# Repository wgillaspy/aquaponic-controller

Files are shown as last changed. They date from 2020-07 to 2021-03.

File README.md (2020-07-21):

# aquaponic-controller

*Currently a trough style hydroponic setup while I work out the hardware and code.  Once the bugs
are fixed and things stabilize, if the space is available, I'll add in some fish.  But right it's
easy enough to grow a decent crop of lettuce with General Hydroponics fertilizer, epsom salt, calcium hydroxide
and some ferrous gluconate iron solution.

This isn't a particularly cheap project to undertake, but the results have been been rewarding.
Fresh, well developed, and bug free lettuce and herbs.  Being in South Carolina, lettuce isn't
one of those things we get to grow well in the summer. Simply too hot.  Now we have a surpus for ourselves
and friends.

As with most of my projects, this one involves a raspberry pi and an arduino.  Adding to the cast
is also a Alchitry Au (which I may regret since I can't seen to find any more to order) and several
Atlas Scientific circuits and probes.  Binding those circuits to the raspberry pi is a whitebox labs
Tentacle T3.

[The full bill of materials is here.](BOM.MD)

I really can't speak highly enough of the Atlas Scientific ecosystem.  With a little looking around
I was able to find enough information to drive the circuits with javascript, pop them into a NodeJs
project and then pop that into a docker container.

I prefer to run ubuntu server on my raspberry pi, so there was some additional configuration
I needed to enable the I2C interface.

If you dig ansible, you can use this block to help figure out how to enable I2C on a ubuntu install.
I've also included the two files that are copied in the root of this project.

```yaml
    - name: Install i2c-tools
      apt:
        name: i2c-tools
        state: present
        update_cache: yes
      become: yes
    - name: Copy modules file.
      copy:
        src: modules
        dest: /etc/modules
        mode: 0644
      become: yes
    - name: Copy the usrcfg.txt to the firmware directory.
      copy:
        src: usercfg.txt
        dest: /boot/firmware/usercfg.txt
        mode: 0655
      become: yes
```

The [parts](parts) directory contains all the .stls and Alibre files that I used to mount things.  Nothing is refined, but all 
the electronics and pumps mount to DIN rails.  The probes and float switches mount to 1"PVC pipes in the sump.

 #### State of the project.
- pH is monitored and adjusted upward with calcium hydroxide solution in tap water.  The clear liquid between the calcium sediment
  and crust is dosed using a Milwaukee Dosing controlled through Home Assistant > Phillips Hue > Smart Plug.
- Electrical Conductivity (EC) is monitored and adjusted upward by dosing diluted General Hydroponic fertilizer with an EZO PMP. 
- A diluted mixture of Magnesium (epsom salt) and Iron (ferrous gluconate) is dosed periodically with an EZO PMP.  Iron and Magnesium are not 
  monitored and are simply added on a set schedule.
  
The configuration is pretty strait forward and [available here](src/main/javascript/probe-reader/configuration.json) 

Probes are easily added to the configuration by adding a new distinct element to the probe object.  If the new probe
needs to run some dosing pump, then a rule can be setup in the dosing section with the same distinct element key.

Dosing pumps that run a schedule can be added to the scheduled section of the configuration.

Again, I can't really speak more highly of the Atlas Scientific ecosystem.  Once the boiler plate has been accomplished, its super easy to add additional functionality.

And as usual, I use splunk to log readings.

The arduino currently only holds the Alchitry pins low, but it will eventually be used to automate the periodic water changes.

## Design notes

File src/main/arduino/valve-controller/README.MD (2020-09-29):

lsusb -v | grep -i 'Arduino Uno'

SUBSYSTEMS=="usb", ATTRS{serial}=="7583331353335180F132", SYMLINK+="ino"  > /etc/udev/rules.d/99-usb.rules

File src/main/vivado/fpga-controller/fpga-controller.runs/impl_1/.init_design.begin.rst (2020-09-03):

<?xml version="1.0"?>
<ProcessHandle Version="1" Minor="0">
    <Process Command=".planAhead." Owner="William" Host="DCOMP" Pid="9704">
    </Process>
</ProcessHandle>

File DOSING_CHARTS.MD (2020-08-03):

### Nutrient
| | Type | ml | Conductivity | Total EC | 
|---|--- |----- | --- | ---|
| Full Change | Water |? | 179 | 179 | 
| Full Change | Flora Grow |250 | 400 | 584 | 
| Full Change | Flora Micro |150 | 464 | 1046 |
| Full Change | Flora Cal Mag |50 | ? | ? |

- nutrient_one   = Flora Grow  
- nutrient_three = Flora Micro  
- nutrient_four  = Kelp extract  

### Dosing reservoir mix 840mL (nutrient_two) Iron and Magnesium:  
640ml filtered water  
100ml Mg  
100ml Fe

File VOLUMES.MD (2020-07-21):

### Trough Volume By Depth
| Depth | Gallons  | 
|---|---|
| 3" | 20  |
| 3.5"  | 23  |
| 4" | 26 |
| 5" | 33 |

### Current Volumes:
| | Gallons  | 
|---  |---|
| Upper | 23  |
| Lower | 26 |
| Sump | 33 |
| Total | 59 |

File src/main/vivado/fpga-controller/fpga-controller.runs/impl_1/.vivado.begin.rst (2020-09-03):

<?xml version="1.0"?>
<ProcessHandle Version="1" Minor="0">
    <Process Command="vivado.bat" Owner="William" Host="DCOMP" Pid="14076" HostCore="8" HostMemory="017047703552">
    </Process>
</ProcessHandle>
<?xml version="1.0"?>
<ProcessHandle Version="1" Minor="0">
    <Process Command="vivado.bat" Owner="William" Host="DCOMP" Pid="6972" HostCore="8" HostMemory="017047703552">
    </Process>
</ProcessHandle>

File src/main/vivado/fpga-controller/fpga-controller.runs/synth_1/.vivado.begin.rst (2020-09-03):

<?xml version="1.0"?>
<ProcessHandle Version="1" Minor="0">
    <Process Command="vivado.bat" Owner="William" Host="DCOMP" Pid="12516" HostCore="8" HostMemory="017047703552">
    </Process>
</ProcessHandle>

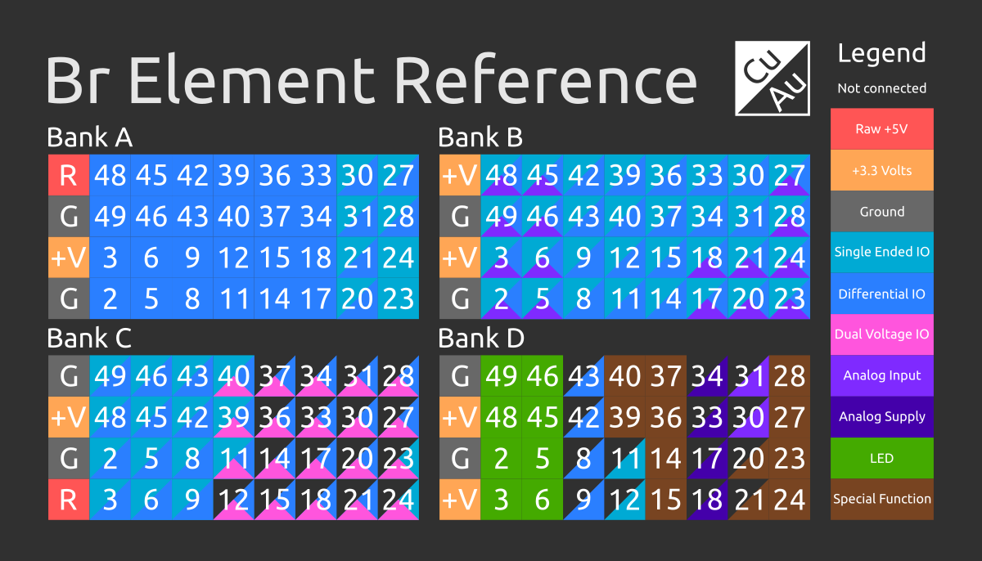
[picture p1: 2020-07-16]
documents/br_front.png

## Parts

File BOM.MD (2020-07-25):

#### Things:
- [Horizontal Leg tank](https://www.tractorsupply.com/tsc/product/horizontal-leg-tank-65-gal) with the top trimmed off. (used)
- Costco Industrial Storage Rack $159.00 
- [Trough Liner](https://farmplasticsupply.com/hydroponics?product_id=474)                   $36.99
- [Blue Line Pump](https://www.championlighting.com/blueline_40_hd_external_water_pump.html) $212.00
- Plywood and 1/8 Boards $80.00
- Raspberry Pi 3b+ (On hand)
- [Milwaukee Dosing pump](https://milwaukeeinstruments.com/milwaukee-instruments-mp810-dosing-pump-for-ph-controller/) x $87.00
- [Smart Plugs](https://www.amazon.com/gp/product/B07SQGG8Z7/ref=ppx_yo_dt_b_asin_title_o08_s00?ie=UTF8&psc=1) (2) $34.99
- [Phlizon 600W LED](https://www.amazon.com/gp/product/B0752CL6KJ/ref=ppx_yo_dt_b_asin_title_o08_s00?ie=UTF8&psc=1) x 3 $239.97
- [T5 HO 4FT 4 Lamp Horticultural Fixture – Red Bloom Spectrum](https://www.activegrowled.com/hydroponic-supplies/t5-ho-4ft-4-lamp-horticultural-fixture-red-bloom-spectrum/) x 2 $438.00
- [T8 HO 4FT 4 Lamp Horticultural Fixture – Sun White Spectrum](https://www.activegrowled.com/hydroponic-supplies/t8-ho-4ft-4-lamp-horticultural-fixture-sun-white-spectrum/) x 2 $438.00
- [T8 HO 2FT 4 Lamp Horticultural Fixture – Red Bloom Spectrum](https://www.activegrowled.com/hydroponic-supplies/t8-ho-2ft-4-lamp-horticultural-fixture-red-bloom-spectrum/) x 2 $270.00
- [U.S. Solid Stainless Steel Electrical Ball Valve 2 Wire Reverse Polarity](https://ussolid.com/u-s-solid-motorized-ball-valve-1-stainless-steel-electrical-ball-valve-with-full-port-9-24-v-dc-2-wire-reverse-polarity.html) x 1 52.99
- [U.S. Solid Motorized Ball Valve 2 Wire Auto Return](https://ussolid.com/u-s-solid-motorized-ball-valve-1-stainless-steel-electrical-ball-valve-with-full-port-9-24-v-ac-dc-2-wire-auto-return.html) x 2 $125.98

Atlas Scientific specific products:
- [EZO-PMP™ Embedded Dosing Pump](https://atlas-scientific.com/peristaltic/) × 2 $170.00
- [EZO™ RTD Temperature Circuit](https://atlas-scientific.com/temperature/) × 1	  $28.00
- [PT-1000 Temperature Probe](https://atlas-scientific.com/temperature/) × 1	      $20.00
- [Whitebox Labs Tentacle T3](https://atlas-scientific.com/carrier-boards/whitebox-labs-tentacle-t3/) × 2	     $210.00
- [EZO™ pH Circuit](https://atlas-scientific.com/ph/) x 1                 $40.00
- [Lab Grade pH Probe](https://atlas-scientific.com/ph/) x 1              $75.00
- [EZO™ Conductivity Circuit](https://atlas-scientific.com/conductivity/)  x 1      $60.00
- [Conductivity Probe K 1.0](https://atlas-scientific.com/conductivity/)   x 1     $139.00

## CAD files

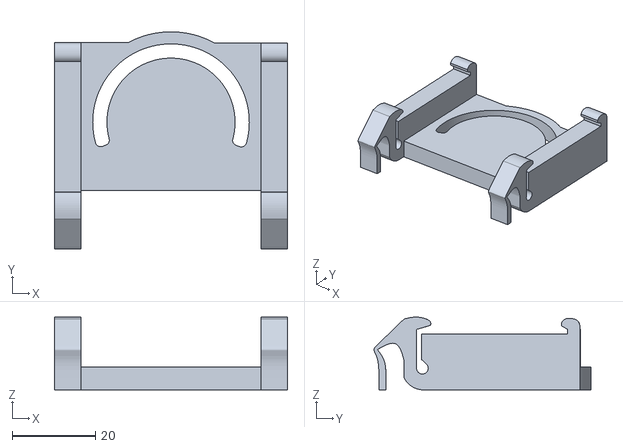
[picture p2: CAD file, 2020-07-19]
parts/PumpAssembly.stl
55.9 x 52.1 x 17.5

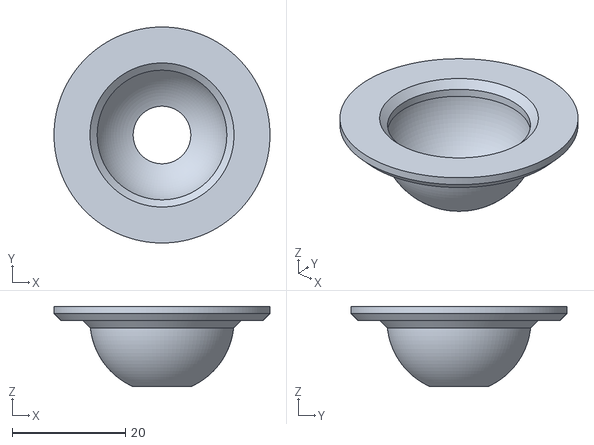
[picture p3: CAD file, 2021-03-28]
parts/Basket.stl
38.1 x 38.1 x 14.2

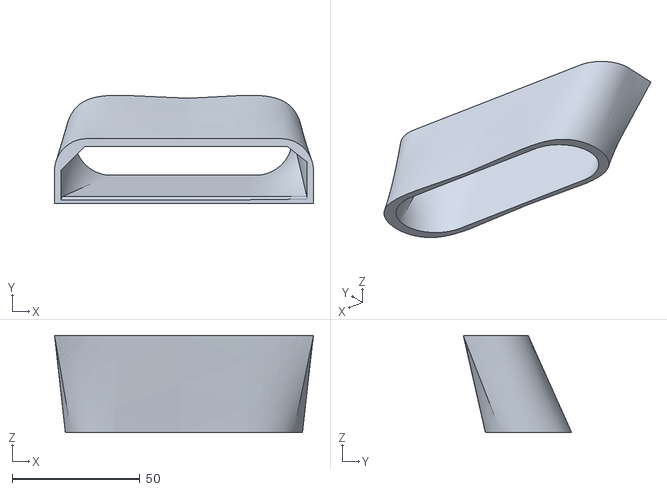
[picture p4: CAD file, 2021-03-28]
parts/Cleaner/FrontSiphone.stl
101.5 x 42.5 x 38.1

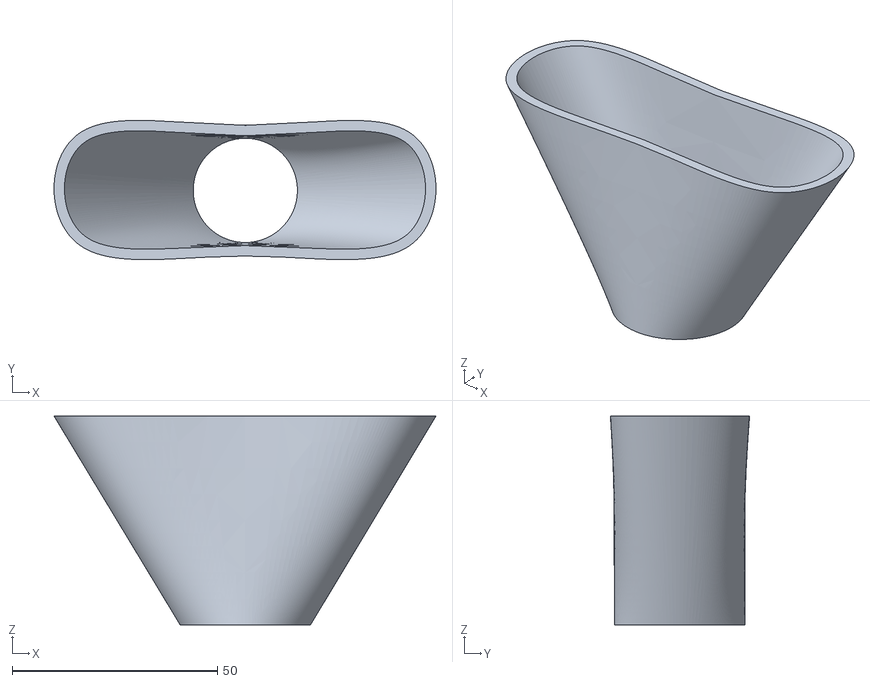
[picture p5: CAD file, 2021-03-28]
parts/Cleaner/RearSiphon.stl
93.0 x 33.9 x 50.8

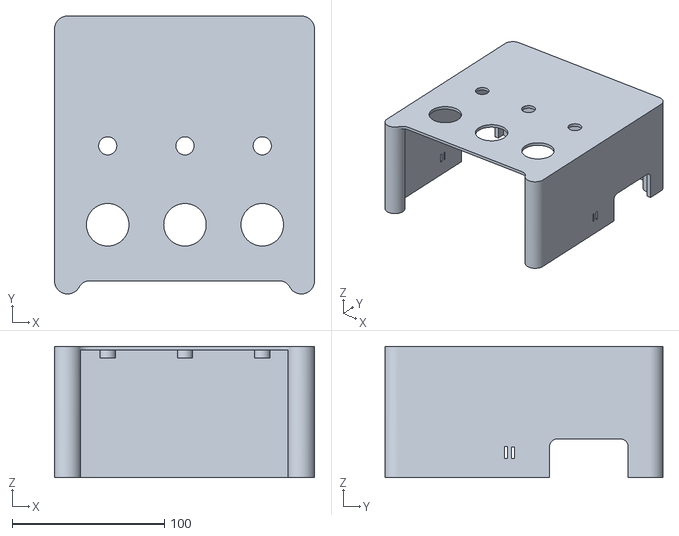
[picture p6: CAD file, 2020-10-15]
parts/ControlBoxLidWSkirt.stl
170.9 x 182.7 x 86.4

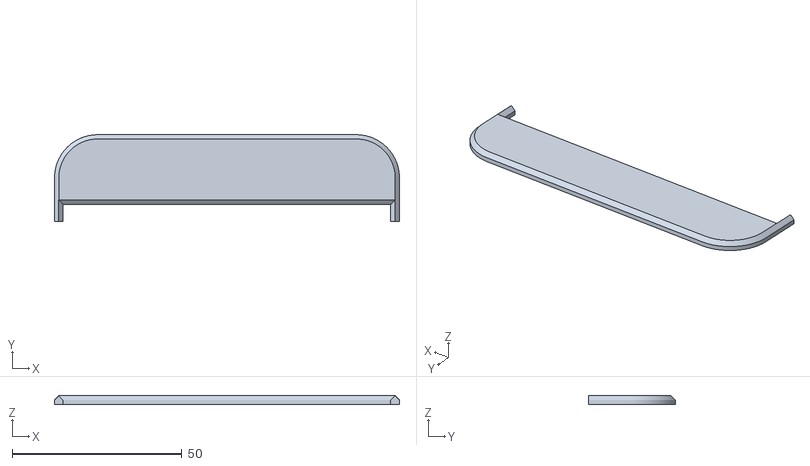
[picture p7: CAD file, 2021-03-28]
parts/Cleaner/FrontCover.stl
101.5 x 25.5 x 2.54

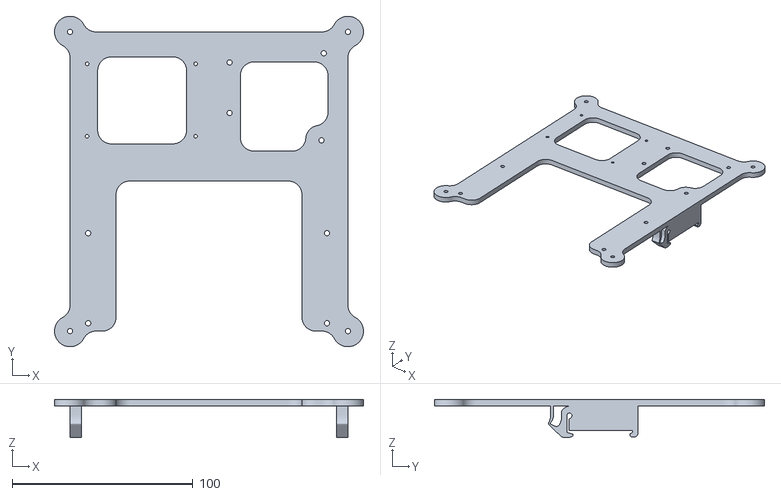
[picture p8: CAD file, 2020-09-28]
parts/ValveControlBackPlate.stl
170.9 x 182.7 x 21.3

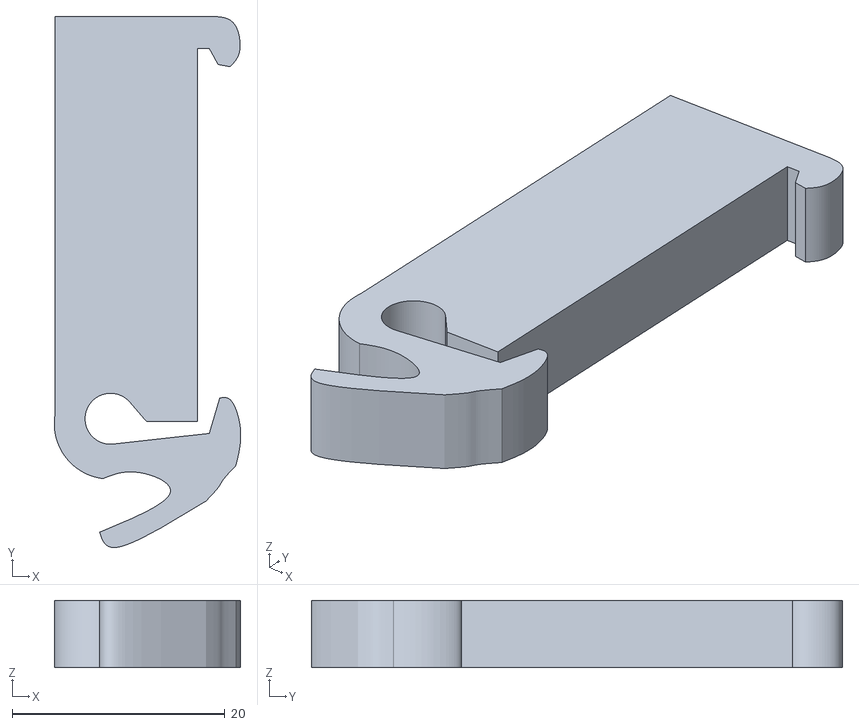
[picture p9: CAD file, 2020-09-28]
parts/DIN_RAIL_MOUNT.stl
17.5 x 50.0 x 6.35

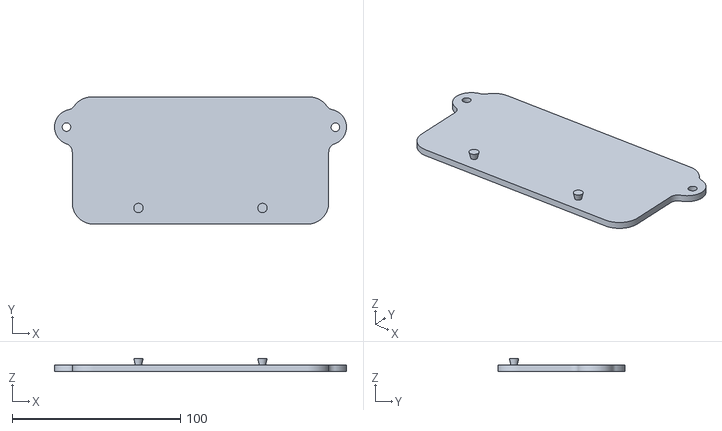
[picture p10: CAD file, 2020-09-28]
parts/Ubiq8PortMount.stl
173.5 x 75.6 x 7.62

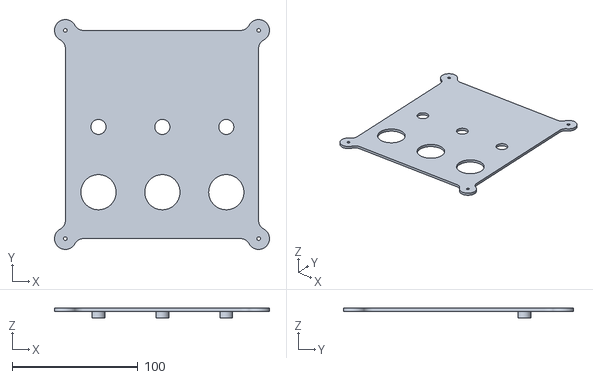
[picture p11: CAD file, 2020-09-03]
parts/ControlBoxLid.stl
170.9 x 182.7 x 7.62

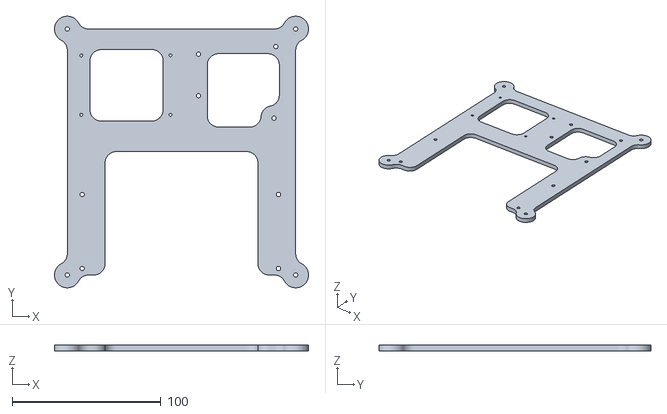
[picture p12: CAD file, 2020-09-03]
parts/ArduinoAlchitryRelayProto.stl
170.9 x 182.7 x 3.81

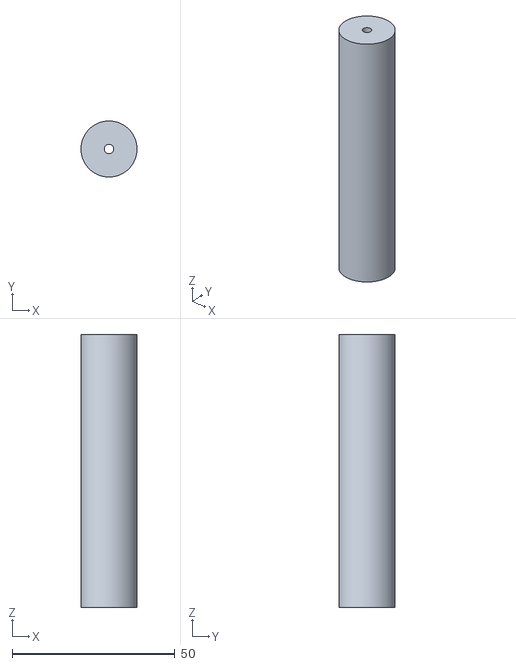
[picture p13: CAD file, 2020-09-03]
parts/Riser.stl
17.2 x 17.2 x 83.8

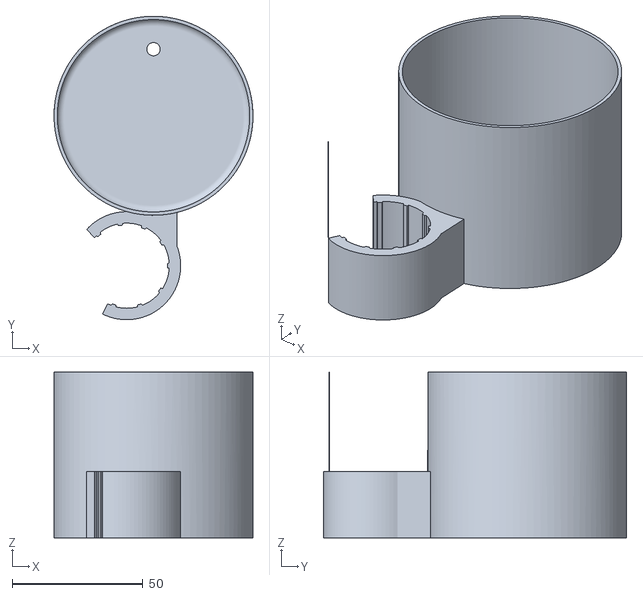
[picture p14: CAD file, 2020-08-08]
parts/floatWaveProtector.stl
76.2 x 116.2 x 63.5

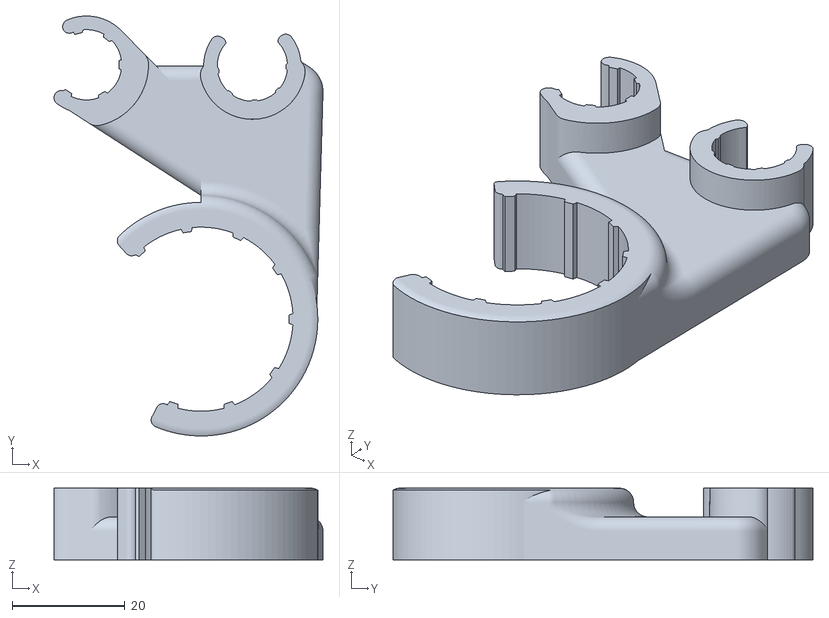
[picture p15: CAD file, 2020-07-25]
parts/probePipeHold.stl
47.6 x 74.4 x 12.7

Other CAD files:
parts/floatPipeHold.stl
parts/pipeHold.stl
parts/pipeTop.stl
parts/PlateDINAssm.stl
parts/8ch_relay_board.stl
parts/MotorMount.stl
parts/Washer.stl
parts/airlineConnector.stl
parts/alchitryAuPlate.stl
parts/alchitry_din.stl

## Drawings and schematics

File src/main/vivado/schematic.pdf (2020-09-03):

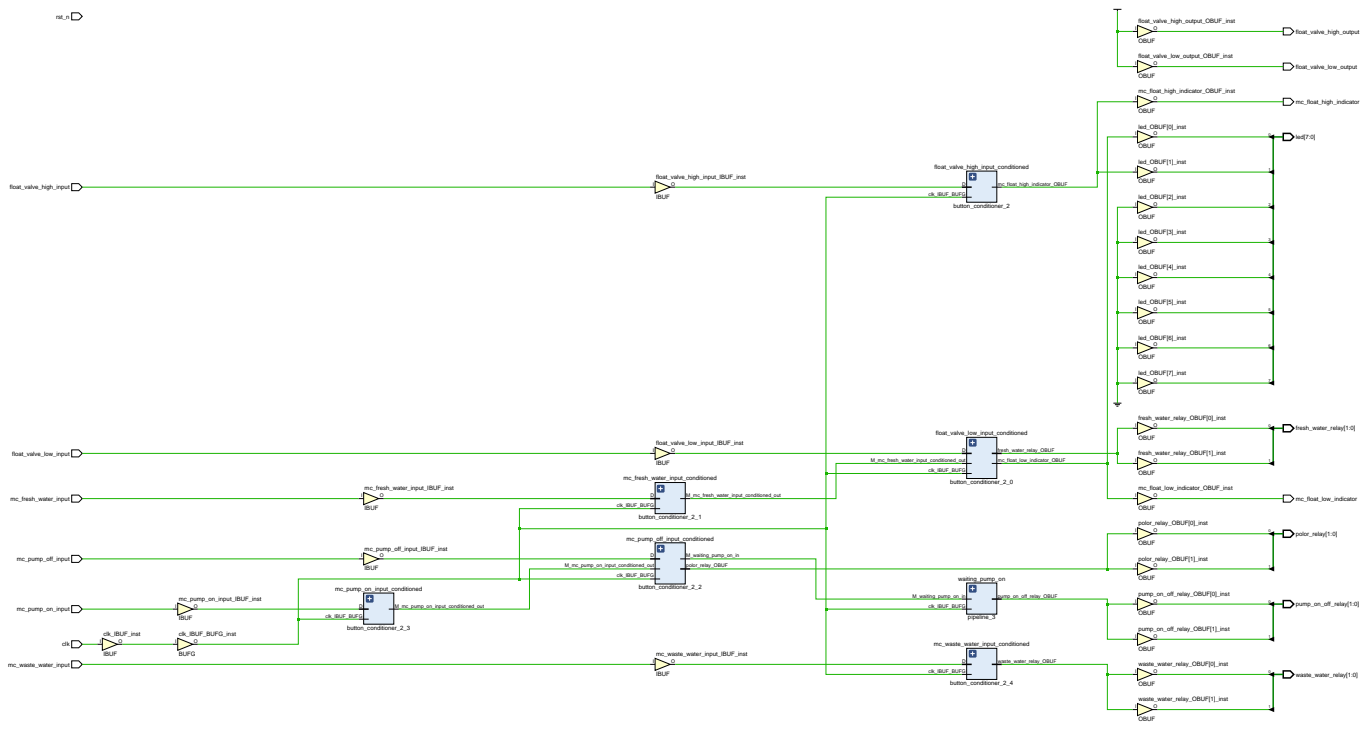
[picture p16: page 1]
float_valve_high_input; float_valve_low_input; mc_fresh_water_input; mc_pump_off_input; mc_pump_on_input; clk; mc_waste_water_input; clk_IBUF_inst; IBUF; mc_pump_on_input_IBUF_inst; clk_IBUF_BUFG_inst; BUFG; mc_fresh_water_input_IBUF_inst; mc_pump_off_input_IBUF_inst; button_conditioner_2_3; clk_IBUF_BUFG; float_valve_high_input_IBUF_inst; float_valve_low_input_IBUF_inst; mc_fresh_water_input_conditioned; button_conditioner_2_1; M_mc_fresh_water_input_conditioned_out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

polor_relay_OBUF

mc_pump_on_input_conditioned | M_mc_pump_on_input_conditioned_out

clk_IBUF_BUFG | M_waiting_pump_on_in | waiting_pump_on

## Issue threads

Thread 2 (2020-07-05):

Change pH dosing to be a time based process rather than waiting on polling to turn it back off.

wgillaspy, 2020-07-05:

wgillaspy, 2021-03-28:
Fixed with ezo dosing pump.

Closed 2021-03-28.

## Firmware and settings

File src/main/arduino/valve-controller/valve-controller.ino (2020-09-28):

#include <ArduinoJson.h>

#define VALVE_OPEN_CLOSE_DELAY 10000
#define WAIT_DELAY 100


#define LED_AND_POWER_INDICATOR           13

#define LED_ONE   A5
#define LED_TWO   A4
#define LED_THREE A3

int LED_VALUE = 130;

// The valves
#define FRESH_WATER_VALVE                 12
#define WASTE_WATER_VALVE                 11
#define FLOW_WATER_VALVE_POLARITY         10
#define FLOW_WATER_VALVE_ON_OFF            9

// The buttons
#define BUTTON_GREEN   A0
#define BUTTON_YELLOW  A1
#define BUTTON_RED     A2

// The float switch inputs
#define FLOAT_SWITCH_LOWER 8
#define FLOAT_SWITCH_UPPER 7


// OLD BELOW / USED ABOVE

boolean flowWaterStatus = true;

boolean waterChange = false;

int loopCount = 0;
int  freshWaterValveState = 0;
int wasteWaterValveState = 0;
int flowValveState = 0;

int floatSwitchLowerValue = 0;
int floatSwitchUpperValue = 0;

boolean override = false;




void setup() {

   Serial.begin(9600);

   pinMode(LED_ONE, OUTPUT);
   pinMode(LED_TWO, OUTPUT);
   pinMode(LED_THREE, OUTPUT);

   analogWrite(LED_ONE, 0);
   analogWrite(LED_TWO, 0);
   analogWrite(LED_THREE, 0);
  
   pinMode(LED_AND_POWER_INDICATOR, OUTPUT);
   digitalWrite(LED_AND_POWER_INDICATOR, HIGH);

   pinMode(FRESH_WATER_VALVE, OUTPUT);
   digitalWrite(FRESH_WATER_VALVE, LOW);

   pinMode(WASTE_WATER_VALVE, OUTPUT);
   digitalWrite(WASTE_WATER_VALVE, LOW);

   pinMode(FLOW_WATER_VALVE_POLARITY, OUTPUT);
   digitalWrite(FLOW_WATER_VALVE_ON_OFF, LOW);

   pinMode(FLOW_WATER_VALVE_ON_OFF, OUTPUT);
   digitalWrite(FLOW_WATER_VALVE_ON_OFF, LOW);

   pinMode(BUTTON_GREEN, INPUT);
   pinMode(BUTTON_YELLOW, INPUT);
   pinMode(BUTTON_RED, INPUT);

   pinMode(FLOAT_SWITCH_LOWER, INPUT);
   pinMode(FLOAT_SWITCH_UPPER, INPUT);

   turnOnFlowValve();
}

void loop() {

  loopCount++;
  delay(WAIT_DELAY);

  if (Serial.available() > 0) {
    // read the incoming byte:
    String incomingJson = Serial.readString();
    readJsonAndDoAction(incomingJson);
    
  }

   floatSwitchLowerValue = digitalRead(FLOAT_SWITCH_LOWER);
   floatSwitchUpperValue = digitalRead(FLOAT_SWITCH_UPPER);
   
   int buttonGreenValue = digitalRead(BUTTON_GREEN);
   int buttonYellowValue = digitalRead(BUTTON_YELLOW);
   int buttonRedValue = digitalRead(BUTTON_RED);

   if (buttonGreenValue > 0) {
     override = false;
     toggleFreshWaterValue(buttonGreenValue);
   } else {
     if (!override) {
      toggleFreshWaterValue(buttonGreenValue);
     }
   }

   if (buttonYellowValue > 0) {
     override = false;
     if (flowWaterStatus) {
       turnOffFlowValve();
     } else {
       turnOnFlowValve();
     }
   }

   if (buttonRedValue > 0) {
     override = false;
     toggleWasteWaterValue(buttonRedValue);
   } else {
    if (!override) {
     toggleWasteWaterValue(buttonRedValue);
    }
   }

   if (loopCount > 10) {
     serialWriteJsonValues();
     loopCount = 0;
  }
}

void indicatorLedOn(int LED) {
  analogWrite(LED, LED_VALUE);
}

void indicatorLedOff(int LED) {
  analogWrite(LED, 0);
}

void readJsonAndDoAction(String inputJson) {
    StaticJsonDocument<400> doc;
    DeserializationError error = deserializeJson(doc, inputJson);
    // Test if parsing succeeds.
    if (error) {
      Serial.print(F("deserializeJson() failed: "));
      Serial.println(error.c_str());
      return;
    }
    int desiredflowValveState = doc["fvs"];
    int desiredFreshwaterValveState = doc["fws"];
    int desiredWasteWaterValveState = doc["wws"];;



    toggleFreshWaterValue(desiredFreshwaterValveState);
    toggleWasteWaterValue(desiredWasteWaterValveState);

    if (desiredflowValveState > 0) {
      turnOnFlowValve();
    } else {
      turnOffFlowValve();
    }

    override = true;

}

void serialWriteJsonValues() {
      String sendJson = "";

      String floatSwitchLowerJson = getJsonPair("fsl", floatSwitchLowerValue);
      String floatSwitchUpperJson = getJsonPair("fsu", floatSwitchUpperValue);
      String flowValveStateJson = getJsonPair("fvs",   flowValveState);

      String freshWaterValveStateJson = getJsonPair("fws", freshWaterValveState);
      String wasteWaterValveStateJson = getJsonPair("wws", wasteWaterValveState);

      sendJson = addToJsonString(sendJson, floatSwitchLowerJson);
      sendJson = addToJsonString(sendJson, floatSwitchUpperJson);
      sendJson = addToJsonString(sendJson, flowValveStateJson);
      sendJson = addToJsonString(sendJson, freshWaterValveStateJson);
      sendJson = addToJsonString(sendJson, wasteWaterValveStateJson);

      Serial.println(sendJson);
}

void toggleFreshWaterValue(int state) {
    if (state > 0) {
      indicatorLedOn(LED_ONE);
      digitalWrite(FRESH_WATER_VALVE, HIGH);
      
    } else {
      indicatorLedOff(LED_ONE);
      digitalWrite(FRESH_WATER_VALVE, LOW);
    }
    freshWaterValveState = state;
}

void toggleWasteWaterValue(int state) {
    if (state > 0) {
      indicatorLedOn(LED_TWO);
      digitalWrite(WASTE_WATER_VALVE, HIGH);
      
    } else {
      indicatorLedOff(LED_TWO);
      digitalWrite(WASTE_WATER_VALVE, LOW);
    }
    wasteWaterValveState = state;
}


void turnOffFlowValve() {
    indicatorLedOn(LED_THREE);
    digitalWrite(FLOW_WATER_VALVE_ON_OFF, LOW);
    delay(WAIT_DELAY);
    digitalWrite(FLOW_WATER_VALVE_POLARITY, LOW);
    delay(WAIT_DELAY);
    digitalWrite(FLOW_WATER_VALVE_ON_OFF, HIGH);
    delay(VALVE_OPEN_CLOSE_DELAY);
    digitalWrite(FLOW_WATER_VALVE_ON_OFF, LOW);
    flowWaterStatus = false;
    flowValveState = 0;
}

void turnOnFlowValve() {
    indicatorLedOff(LED_THREE);
    digitalWrite(FLOW_WATER_VALVE_ON_OFF, LOW);
    delay(WAIT_DELAY);
    digitalWrite(FLOW_WATER_VALVE_POLARITY, HIGH);
    delay(WAIT_DELAY);
    digitalWrite(FLOW_WATER_VALVE_ON_OFF, HIGH);
    delay(VALVE_OPEN_CLOSE_DELAY);
    digitalWrite(FLOW_WATER_VALVE_ON_OFF, LOW);
    digitalWrite(FLOW_WATER_VALVE_POLARITY, LOW);
    flowWaterStatus = true;
    flowValveState = 1;
}

String addToJsonString(String json, String add_json) {
  if (json.length() == 0) {
     return "{" + add_json + "}";
  } else {
    json.remove(json.length() - 1);
    return json + "," + add_json + "}";
  }
}

String getJsonPair(String name, String value) {
  String json = "\"" + name + "\":\"";
  json.concat(value);
  json.concat("\"");
  return json;
}

String getJsonPair(String name, float value) {
  String json = "\"" + name + "\":\"";
  json.concat(value);
  json.concat("\"");
  return json;
}

String getJsonPair(String name, double value) {
  String json = "\"" + name + "\":\"";
  json.concat(value);
  json.concat("\"");
  return json;
}

String getJsonPair(String name, int value) {
  String json = "\"" + name + "\":";
  json.concat(value);
  return json;
}

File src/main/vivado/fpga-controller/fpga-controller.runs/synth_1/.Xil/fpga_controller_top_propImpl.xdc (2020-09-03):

set_property SRC_FILE_INFO {cfile:D:/projects/aquaponic-controller/src/main/vivado/fpga-controller/fpga-controller.srcs/constrs_1/imports/components/alchitry.xdc rfile:../../../fpga-controller.srcs/constrs_1/imports/components/alchitry.xdc id:1} [current_design]
set_property SRC_FILE_INFO {cfile:D:/projects/aquaponic-controller/src/main/vivado/fpga-controller/fpga-controller.srcs/constrs_1/imports/alchitryau/valves.xdc rfile:../../../fpga-controller.srcs/constrs_1/imports/alchitryau/valves.xdc id:2} [current_design]
set_property src_info {type:XDC file:1 line:3 export:INPUT save:INPUT read:READ} [current_design]
set_property PACKAGE_PIN N14 [get_ports {clk}]
set_property src_info {type:XDC file:1 line:5 export:INPUT save:INPUT read:READ} [current_design]
set_property PACKAGE_PIN P6 [get_ports {rst_n}]
set_property src_info {type:XDC file:1 line:7 export:INPUT save:INPUT read:READ} [current_design]
set_property PACKAGE_PIN K13 [get_ports {led[0]}]
set_property src_info {type:XDC file:1 line:9 export:INPUT save:INPUT read:READ} [current_design]
set_property PACKAGE_PIN K12 [get_ports {led[1]}]
set_property src_info {type:XDC file:1 line:11 export:INPUT save:INPUT read:READ} [current_design]
set_property PACKAGE_PIN L14 [get_ports {led[2]}]
set_property src_info {type:XDC file:1 line:13 export:INPUT save:INPUT read:READ} [current_design]
set_property PACKAGE_PIN L13 [get_ports {led[3]}]
set_property src_info {type:XDC file:1 line:15 export:INPUT save:INPUT read:READ} [current_design]
set_property PACKAGE_PIN M16 [get_ports {led[4]}]
set_property src_info {type:XDC file:1 line:17 export:INPUT save:INPUT read:READ} [current_design]
set_property PACKAGE_PIN M14 [get_ports {led[5]}]
set_property src_info {type:XDC file:1 line:19 export:INPUT save:INPUT read:READ} [current_design]
set_property PACKAGE_PIN M12 [get_ports {led[6]}]
set_property src_info {type:XDC file:1 line:21 export:INPUT save:INPUT read:READ} [current_design]
set_property PACKAGE_PIN N16 [get_ports {led[7]}]
set_property src_info {type:XDC file:2 line:3 export:INPUT save:INPUT read:READ} [current_design]
set_property PACKAGE_PIN E2 [get_ports {mc_fresh_water_input}]
set_property src_info {type:XDC file:2 line:5 export:INPUT save:INPUT read:READ} [current_design]
set_property PACKAGE_PIN B2 [get_ports {mc_pump_on_input}]
set_property src_info {type:XDC file:2 line:7 export:INPUT save:INPUT read:READ} [current_design]
set_property PACKAGE_PIN F2 [get_ports {mc_pump_off_input}]
set_property src_info {type:XDC file:2 line:9 export:INPUT save:INPUT read:READ} [current_design]
set_property PACKAGE_PIN F4 [get_ports {mc_waste_water_input}]
set_property src_info {type:XDC file:2 line:11 export:INPUT save:INPUT read:READ} [current_design]
set_property PACKAGE_PIN B4 [get_ports {mc_float_low_indicator}]
set_property src_info {type:XDC file:2 line:13 export:INPUT save:INPUT read:READ} [current_design]
set_property PACKAGE_PIN A5 [get_ports {mc_float_high_indicator}]
set_property src_info {type:XDC file:2 line:15 export:INPUT save:INPUT read:READ} [current_design]
set_property PACKAGE_PIN D1 [get_ports {float_valve_low_output}]
set_property src_info {type:XDC file:2 line:18 export:INPUT save:INPUT read:READ} [current_design]
set_property PACKAGE_PIN A2 [get_ports {float_valve_low_input}]
set_property src_info {type:XDC file:2 line:21 export:INPUT save:INPUT read:READ} [current_design]
set_property PACKAGE_PIN E1 [get_ports {float_valve_high_output}]
set_property src_info {type:XDC file:2 line:24 export:INPUT save:INPUT read:READ} [current_design]
set_property PACKAGE_PIN F3 [get_ports {float_valve_high_input}]
set_property src_info {type:XDC file:2 line:27 export:INPUT save:INPUT read:READ} [current_design]
set_property PACKAGE_PIN C7 [get_ports {fresh_water_relay[0]}]
set_property src_info {type:XDC file:2 line:30 export:INPUT save:INPUT read:READ} [current_design]
set_property PACKAGE_PIN D6 [get_ports {fresh_water_relay[1]}]
set_property src_info {type:XDC file:2 line:33 export:INPUT save:INPUT read:READ} [current_design]
set_property PACKAGE_PIN F5 [get_ports {pump_on_off_relay[0]}]
set_property src_info {type:XDC file:2 line:36 export:INPUT save:INPUT read:READ} [current_design]
set_property PACKAGE_PIN G5 [get_ports {pump_on_off_relay[1]}]
set_property src_info {type:XDC file:2 line:39 export:INPUT save:INPUT read:READ} [current_design]
set_property PACKAGE_PIN D4 [get_ports {polor_relay[0]}]
set_property src_info {type:XDC file:2 line:42 export:INPUT save:INPUT read:READ} [current_design]
set_property PACKAGE_PIN E3 [get_ports {polor_relay[1]}]
set_property src_info {type:XDC file:2 line:45 export:INPUT save:INPUT read:READ} [current_design]
set_property PACKAGE_PIN C3 [get_ports {waste_water_relay[0]}]
set_property src_info {type:XDC file:2 line:48 export:INPUT save:INPUT read:READ} [current_design]
set_property PACKAGE_PIN C1 [get_ports {waste_water_relay[1]}]
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

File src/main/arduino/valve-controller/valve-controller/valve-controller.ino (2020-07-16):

#define READ_DELAY 12000
#define WAIT_DELAY 2000

#define FRESH_WATER_VALVE  9
#define PUMP_VALVE_ON 8
#define PUMP_VALVE_OFF 7
#define WASTE_WATER_VALVE  6

#define FLOAT_VALVE_HIGH 5
#define FLOAT_VALVE_HIGH  4

void setup() {
   pinMode(FRESH_WATER_VALVE, OUTPUT);
   pinMode(PUMP_VALVE_ON,     OUTPUT);
   pinMode(PUMP_VALVE_OFF,    OUTPUT);
   pinMode(WASTE_WATER_VALVE,    OUTPUT);

   pinMode(FLOAT_VALVE_HIGH,    INPUT);
   pinMode(FLOAT_VALVE_HIGH,    INPUT);
  
   digitalWrite(FRESH_WATER_VALVE, LOW);
   digitalWrite(PUMP_VALVE_ON,     LOW);
   digitalWrite(PUMP_VALVE_OFF,    LOW);
   digitalWrite(WASTE_WATER_VALVE, LOW);
}

void loop() {

  boolean once = false;

  

//  delay(READ_DELAY);
//  digitalWrite(PUMP_VALVE_OFF, LOW);
//  delay(WAIT_DELAY);
//  digitalWrite(PUMP_VALVE_ON, HIGH);
//  digitalWrite(13, HIGH);
//  delay(READ_DELAY);
//  digitalWrite(PUMP_VALVE_ON, LOW);
//  delay(WAIT_DELAY);
//  digitalWrite(PUMP_VALVE_OFF, HIGH);
//  //digitalWrite(PUMP_VALVE_ON, LOW);
//  //digitalWrite(FRESH_WATER_VALVE, HIGH);
//  digitalWrite(13, LOW);
   delay(READ_DELAY);
}

void waterChange() {


  

    
  
}

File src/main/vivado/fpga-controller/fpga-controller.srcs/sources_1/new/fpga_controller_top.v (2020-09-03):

`timescale 1ns / 1ps
//////////////////////////////////////////////////////////////////////////////////
// Company: 
// Engineer: 
// 
// Create Date: 08/13/2020 06:31:11 PM
// Design Name: 
// Module Name: fpga_controller_top
// Project Name: 
// Target Devices: 
// Tool Versions: 
// Description: 
// 
// Dependencies: 
// 
// Revision:
// Revision 0.01 - File Created
// Additional Comments:
// 
//////////////////////////////////////////////////////////////////////////////////


module fpga_controller_top(
    input clk,
    input rst_n,
    output reg [7:0] led,
    input mc_fresh_water_input,
    input mc_pump_on_input,
    input mc_pump_off_input,
    input mc_waste_water_input,
    output reg mc_float_low_indicator,
    output reg mc_float_high_indicator,
    output reg float_valve_low_output,
    input float_valve_low_input,
    output reg float_valve_high_output,
    input float_valve_high_input,
    output reg [1:0] fresh_water_relay,
    output reg [1:0] waste_water_relay,
    output reg [1:0] pump_on_off_relay,
    output reg [1:0] polor_relay
    );
      reg rst;
  
  wire [1-1:0] M_reset_cond_out;
  reg [1-1:0] M_reset_cond_in;
  reset_conditioner_1 reset_cond (
    .clk(clk),
    .in(M_reset_cond_in),
    .out(M_reset_cond_out)
  );
  wire [1-1:0] M_mc_fresh_water_input_conditioned_out;
  reg [1-1:0] M_mc_fresh_water_input_conditioned_in;
  button_conditioner_2 mc_fresh_water_input_conditioned (
    .clk(clk),
    .in(M_mc_fresh_water_input_conditioned_in),
    .out(M_mc_fresh_water_input_conditioned_out)
  );
  wire [1-1:0] M_mc_waste_water_input_conditioned_out;
  reg [1-1:0] M_mc_waste_water_input_conditioned_in;
  button_conditioner_2 mc_waste_water_input_conditioned (
    .clk(clk),
    .in(M_mc_waste_water_input_conditioned_in),
    .out(M_mc_waste_water_input_conditioned_out)
  );
  wire [1-1:0] M_mc_pump_on_input_conditioned_out;
  reg [1-1:0] M_mc_pump_on_input_conditioned_in;
  button_conditioner_2 mc_pump_on_input_conditioned (
    .clk(clk),
    .in(M_mc_pump_on_input_conditioned_in),
    .out(M_mc_pump_on_input_conditioned_out)
  );
  wire [1-1:0] M_mc_pump_off_input_conditioned_out;
  reg [1-1:0] M_mc_pump_off_input_conditioned_in;
  button_conditioner_2 mc_pump_off_input_conditioned (
    .clk(clk),
    .in(M_mc_pump_off_input_conditioned_in),
    .out(M_mc_pump_off_input_conditioned_out)
  );
  wire [1-1:0] M_float_valve_low_input_conditioned_out;
  reg [1-1:0] M_float_valve_low_input_conditioned_in;
  button_conditioner_2 float_valve_low_input_conditioned (
    .clk(clk),
    .in(M_float_valve_low_input_conditioned_in),
    .out(M_float_valve_low_input_conditioned_out)
  );
  wire [1-1:0] M_float_valve_high_input_conditioned_out;
  reg [1-1:0] M_float_valve_high_input_conditioned_in;
  button_conditioner_2 float_valve_high_input_conditioned (
    .clk(clk),
    .in(M_float_valve_high_input_conditioned_in),
    .out(M_float_valve_high_input_conditioned_out)
  );
  wire [1-1:0] M_waiting_pump_on_out;
  reg [1-1:0] M_waiting_pump_on_in;
  pipeline_3 waiting_pump_on (
    .clk(clk),
    .in(M_waiting_pump_on_in),
    .out(M_waiting_pump_on_out)
  );
  
  always @* begin
    M_reset_cond_in = ~rst_n;
    rst = M_reset_cond_out;
    led = 8'h00;
    polor_relay = 8'hff;
    pump_on_off_relay = 8'hff;
    float_valve_low_output = 8'hff;
    float_valve_high_output = 8'hff;
    M_float_valve_low_input_conditioned_in = float_valve_low_input;
    M_float_valve_high_input_conditioned_in = float_valve_high_input;
    led[0+0-:1] = M_float_valve_low_input_conditioned_out;
    led[1+0-:1] = M_float_valve_high_input_conditioned_out;
    mc_float_low_indicator = M_float_valve_low_input_conditioned_out;
    mc_float_high_indicator = M_float_valve_high_input_conditioned_out;
    M_mc_fresh_water_input_conditioned_in = mc_fresh_water_input;
    M_mc_waste_water_input_conditioned_in = mc_waste_water_input;
    if (M_mc_fresh_water_input_conditioned_out | M_float_valve_low_input_conditioned_out) begin
      fresh_water_relay = 8'h00;
    end else begin
      fresh_water_relay = 8'hff;
    end
    waste_water_relay = ~{2'h2{M_mc_waste_water_input_conditioned_out}};
    M_mc_pump_on_input_conditioned_in = mc_pump_on_input;
    M_mc_pump_off_input_conditioned_in = mc_pump_off_input;
    polor_relay = ~{2'h2{M_mc_pump_off_input_conditioned_out}};
    M_waiting_pump_on_in = (M_mc_pump_on_input_conditioned_out | M_mc_pump_off_input_conditioned_out);
    if (M_waiting_pump_on_out) begin
      pump_on_off_relay[0+0-:1] = 8'h00;
      pump_on_off_relay[1+0-:1] = 8'h00;
    end else begin
      pump_on_off_relay[0+0-:1] = 8'hff;
      pump_on_off_relay[1+0-:1] = 8'hff;
    end
  end
endmodule

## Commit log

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2020-07-04 Fix on off state.
    [index-library.js]
2020-07-16 Documents, logging.
    [8ch_relay_board.stl, PlateDINAssm.stl, alchitryAuPlate.stl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]
2020-07-18 Adding temperature probe.
    [floatPipeHold.stl, pipeHold.stl, probePipeHold.stl]
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2020-07-19 Putting in real values.
    [MotorMount.stl, PumpAssembly.stl, airlineConnector.stl]
2020-07-21 Documentation. Updating the crontab.
    [PlateDINAssm.stl]
2020-07-25 Increasing the mg / fe dosing.
    [floatPipeHold.stl, pipeHold.stl, pipeTop.stl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]
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2020-08-03 Adding additional dosing pumps. Making the dosing function look at arrays so that more than one thing can be dosed based off of a probe reading.
2020-08-03 Fixing function that keeps up with dosing so that more than one pump can dose.
    [index-library.js]
2020-08-03 Fixing function that keeps up with dosing so that more than one pump can dose. Reducing dosing amount per point.
    [index-library.js]
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2020-09-03 Adding new parts and forcing a deployment to update splunk url.
    [ArduinoAlchitryRelayProto.stl, ControlBoxLid.stl, Riser.stl]
2020-09-19 Keep the pH dosing pumps from fighting with one another. Improve logging.
2020-09-28 Redesigned the FPGA code to be simpler. Added buttons and valve logic to the arduino Added input out json value to the arduino's serial. Adding some parts.
    [DIN_RAIL_MOUNT.stl, Ubiq8PortMount.stl, ValveControlBackPlate.stl]
2020-10-15 Updating configuration. Parts
    [ControlBoxLidWSkirt.stl]
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2020-12-13 Bump ini from 1.3.5 to 1.3.8 in /src/main/javascript/probe-reader
    Bumps [ini](https://github.com/isaacs/ini) from 1.3.5 to 1.3.8.
    - [Release notes](https://github.com/isaacs/ini/releases)
    - [Commits](https://github.com/isaacs/ini/compare/v1.3.5...v1.3.8)
2021-01-06 Bump axios from 0.20.0 to 0.21.1 in /src/main/javascript/probe-reader
    Bumps [axios](https://github.com/axios/axios) from 0.20.0 to 0.21.1.
    - [Release notes](https://github.com/axios/axios/releases)
    - [Changelog](https://github.com/axios/axios/blob/v0.21.1/CHANGELOG.md)
    - [Commits](https://github.com/axios/axios/compare/v0.20.0...v0.21.1)
2021-03-28 Increasing the target conductivity to reduce root shock. Checking in parts.
    [Basket.stl, FrontCover.stl, FrontSiphone.stl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]
2021-05-10 Bump url-parse from 1.4.7 to 1.5.1 in /src/main/javascript/probe-reader
    Bumps [url-parse](https://github.com/unshiftio/url-parse) from 1.4.7 to 1.5.1.
    - [Release notes](https://github.com/unshiftio/url-parse/releases)
    - [Commits](https://github.com/unshiftio/url-parse/compare/1.4.7...1.5.1)
2021-05-11 Bump lodash from 4.17.20 to 4.17.21 in /src/main/javascript/probe-reader
    Bumps [lodash](https://github.com/lodash/lodash) from 4.17.20 to 4.17.21.
    - [Release notes](https://github.com/lodash/lodash/releases)
    - [Commits](https://github.com/lodash/lodash/compare/4.17.20...4.17.21)
2022-02-13 Bump follow-redirects in /src/main/javascript/probe-reader
    Bumps [follow-redirects](https://github.com/follow-redirects/follow-redirects) from 1.13.1 to 1.14.8.
    - [Release notes](https://github.com/follow-redirects/follow-redirects/releases)
    - [Commits](https://github.com/follow-redirects/follow-redirects/compare/v1.13.1...v1.14.8)
    ---
    updated-dependencies:
    - dependency-name: follow-redirects
    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
2022-02-27 Bump url-parse from 1.5.1 to 1.5.10 in /src/main/javascript/probe-reader
    Bumps [url-parse](https://github.com/unshiftio/url-parse) from 1.5.1 to 1.5.10.
    - [Commits](https://github.com/unshiftio/url-parse/compare/1.5.1...1.5.10)
    - dependency-name: url-parse
    dependency-type: indirect
    ...
    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
2022-03-28 Bump minimist from 1.2.5 to 1.2.6 in /src/main/javascript/probe-reader
    Bumps [minimist](https://github.com/substack/minimist) from 1.2.5 to 1.2.6.
    - [Release notes](https://github.com/substack/minimist/releases)
    - [Commits](https://github.com/substack/minimist/compare/1.2.5...1.2.6)
    - dependency-name: minimist
    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
2022-07-07 Bump moment from 2.29.1 to 2.29.4 in /src/main/javascript/probe-reader
    Bumps [moment](https://github.com/moment/moment) from 2.29.1 to 2.29.4.
    - [Release notes](https://github.com/moment/moment/releases)
    - [Changelog](https://github.com/moment/moment/blob/develop/CHANGELOG.md)
    - [Commits](https://github.com/moment/moment/compare/2.29.1...2.29.4)
    - dependency-name: moment
    dependency-type: direct:production
    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
2022-08-31 Bump moment-timezone in /src/main/javascript/probe-reader
    Bumps [moment-timezone](https://github.com/moment/moment-timezone) from 0.5.31 to 0.5.37.
    - [Release notes](https://github.com/moment/moment-timezone/releases)
    - [Changelog](https://github.com/moment/moment-timezone/blob/develop/changelog.md)
    - [Commits](https://github.com/moment/moment-timezone/compare/0.5.31...0.5.37)
    - dependency-name: moment-timezone
    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
2022-09-14 Bump axios from 0.21.1 to 0.21.2 in /src/main/javascript/probe-reader
    Bumps [axios](https://github.com/axios/axios) from 0.21.1 to 0.21.2.
    - [Changelog](https://github.com/axios/axios/blob/v0.21.2/CHANGELOG.md)
    - [Commits](https://github.com/axios/axios/compare/v0.21.1...v0.21.2)
    - dependency-name: axios
    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
